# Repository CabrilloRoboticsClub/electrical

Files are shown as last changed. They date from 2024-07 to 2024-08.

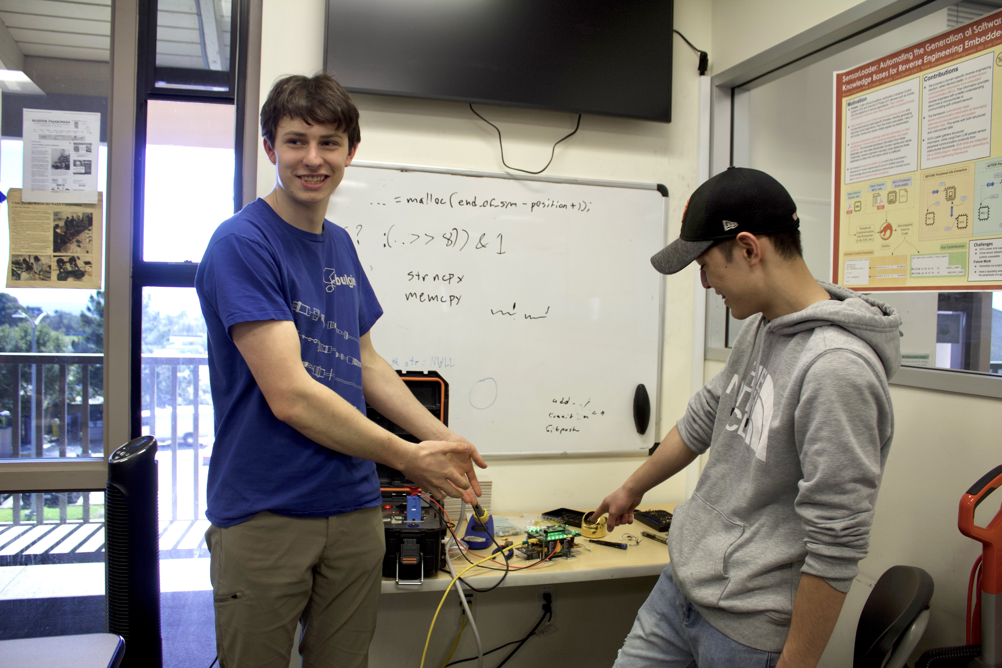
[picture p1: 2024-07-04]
Photos/Electrical_Team_Cellbrating_First_Full_Power_UpWithNoSmoke.jpg

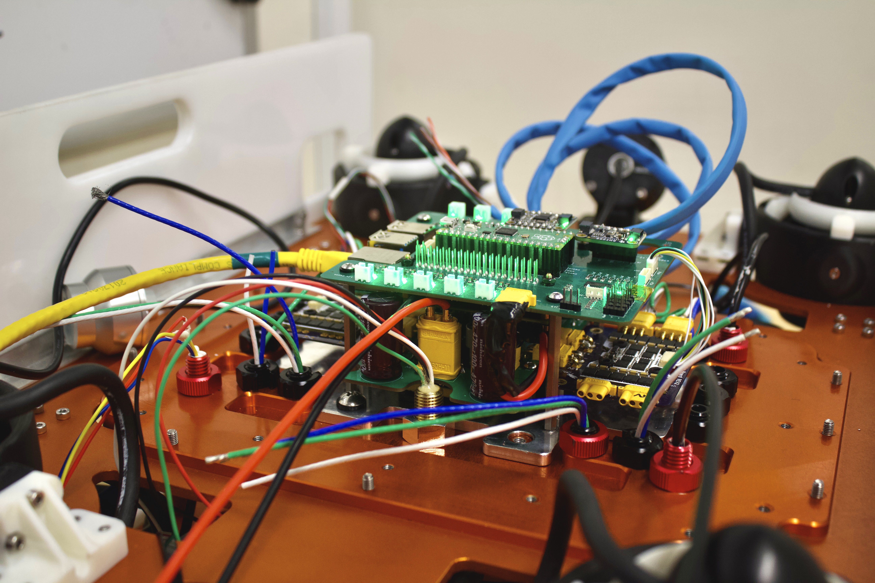
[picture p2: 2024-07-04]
Photos/FirstPowerUpOnROV.jpg

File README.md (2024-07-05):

# MATE ROV Electrical Stack for 2024 ROV Seahawk II

## Overview
This year, we decided to develop a stack of custom boards for the first time. We made this decision to reduce the size and weight of the Seahawk II while also improving overall durability, reliability, and power consumption. In the past, wiring harnesses were a significant point of failure, so we aimed to reduce their use.

## Intorduction
ectrical_Box_Stack_Overview Photo


The Seahawk II electrical stack focuses on high integration. We reduced the number of boards to three, which all connect seamlessly. This minimized space requirements. While the R&D expenses for developing these boards were high, the completed stack is incredibly reliable and significantly reduces costs compared to off-the-shelf options.

## For exstive documetaion go to the wiki

https://github.com/CabrilloRoboticsClub/electrical/wiki

### Members of 2024 electrical team:
- Isaac Wax
- Isaac Eda

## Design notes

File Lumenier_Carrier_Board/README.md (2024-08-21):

# Lumenier ESC Carrier Board
https://github.com/CabrilloRoboticsClub/electrical/wiki/ESC-Carrier-Board

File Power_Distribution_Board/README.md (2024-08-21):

# Power Distrubtion Board
https://github.com/CabrilloRoboticsClub/electrical/wiki/Power-Distribution-Boad

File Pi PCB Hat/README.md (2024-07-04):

# Pi PCB Hat

https://github.com/CabrilloRoboticsClub/electrical/wiki/Pi-Hat-PCB

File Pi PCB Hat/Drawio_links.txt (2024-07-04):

RPI Hat
https://drive.google.com/file/d/1-mpWdMjtuBn4qCpJHgUvGb3abJFzCt9e/view?usp=sharing

Bus lines Pi Hat PCB
https://drive.google.com/file/d/16jqgarMsz4_aKGhgsrGLv56VGpTJN2zc/view?usp=sharing

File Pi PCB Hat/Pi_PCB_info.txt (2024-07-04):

This .txt serves as general purpose information, as well as a checklist. Therefore every major connection/interaction must be listed here. by Isaac Eda

RPI Headers
- This is the interface for the Raspberry Pi 4(RPi 4)
- Supply Power: The Pi itself is powered by 5V through its USB port. No need for power input through the Pi hat PCB board.
- I2C: The two I2C ports, SDA and SCL are extended through the PCB as BUS lines. Multiple devices connect to this BUS.
- UART: The Pico W is connected to the Pi 4 via UART
- Power Supplied(to other devices): Supplies 3.3V logic power to the BNO05 and BME280. Also supplies 5V logic power to the PCA9685 PWM chip.
- Signal: Handles multiple inputs/outputs via GPIO to multiple devices, including; GPIO output for Power Switching Mosfets, output for BNO05 reset, input for BNO05 interrupt pin, input for BME280 Data, output for Pico W reset transistor switch, output for PCA9685 OE(output enable) pin.

Power Switching
- This is for switching on/off the relatively large power from the Power Board PCB, whether it's 12V or 5V. Multiples of this circuit may be present on the Pi PCB. Multiple may even branch out from the same power BUS line.
- Supply Power: Either 12V or 5V, supplied by the Power board PCB. 
- Signal: takes GPIO from RPi 4, to turn mosfet on/off
- Power Supplied: (Multiple)Solenoid valves for switching pneumatics, miscellaneous 5V tooling.

BNO05
- Inertial Measurement Unit(IMU)
- Supply Power: Takes 3.3V logic power
- I2C: Connected via I2C SDA and SCL
- Signal: GPIO input for reset, GPIO output for configurable Hardware interrupt. Also a solderable jumper pad connected to supply power to change I2C address is included on the Pi hat PCB.

BME280
- Humidity Sensor
- Supply Power: Takes 3.3V logic power
- I2C: Connected via I2C SDA and SCL
- Signal: GPIO output for data

PICO W Headers
- Supply Power: The Pico W is powered by 5V through its USB port. No need for input power through the Pi hat PCB board. 
- I2C: Connected via I2C SDA and SCL
- UART: Connected to RPi 4 via UART RX and TX
- Power Supplied(to other devices): 

PCA9685 PWM
-

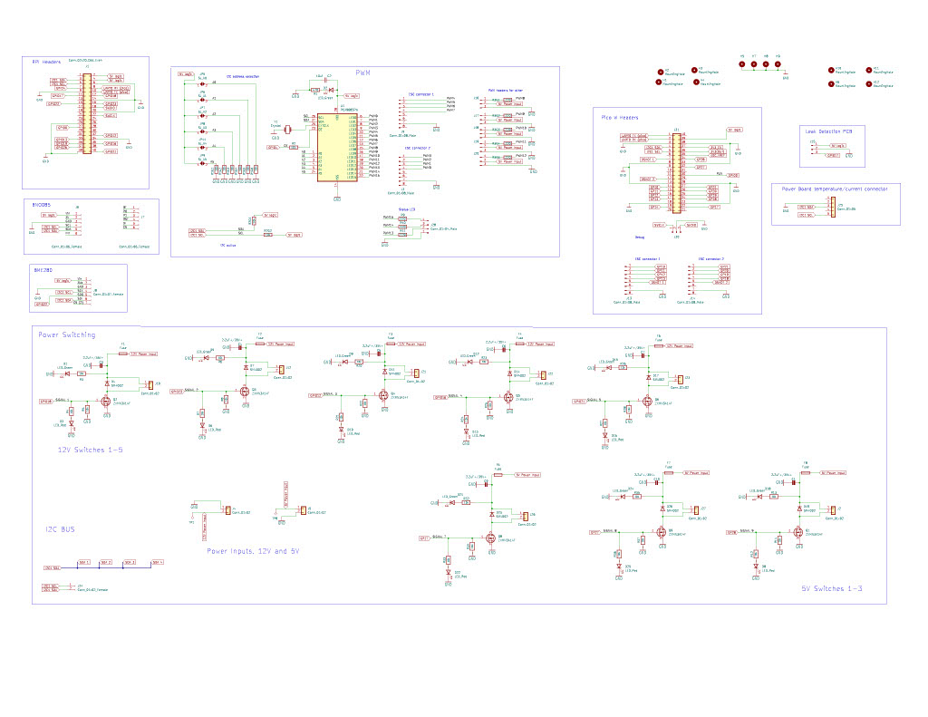
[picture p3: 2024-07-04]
Pi PCB Hat/Pi_Hat_Schematic.jpg

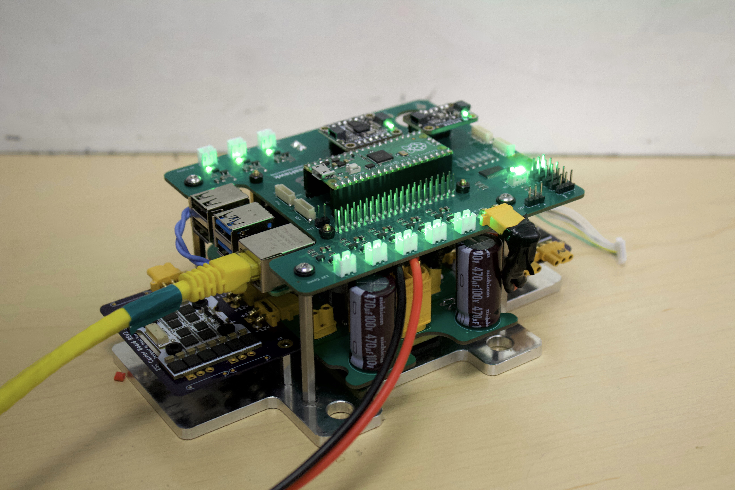
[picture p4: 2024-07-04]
Photos/FirstPowerUp.jpg

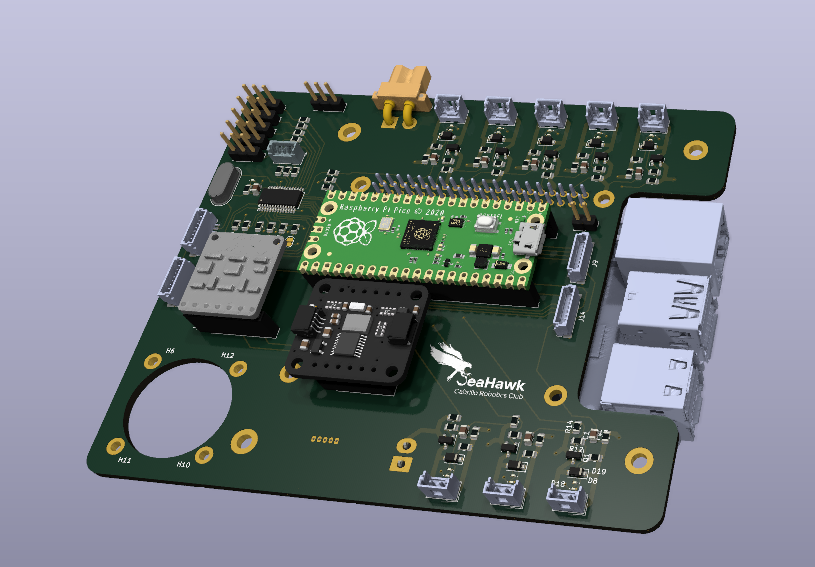
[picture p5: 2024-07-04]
Photos/Screenshot 2024-05-08 224635.png

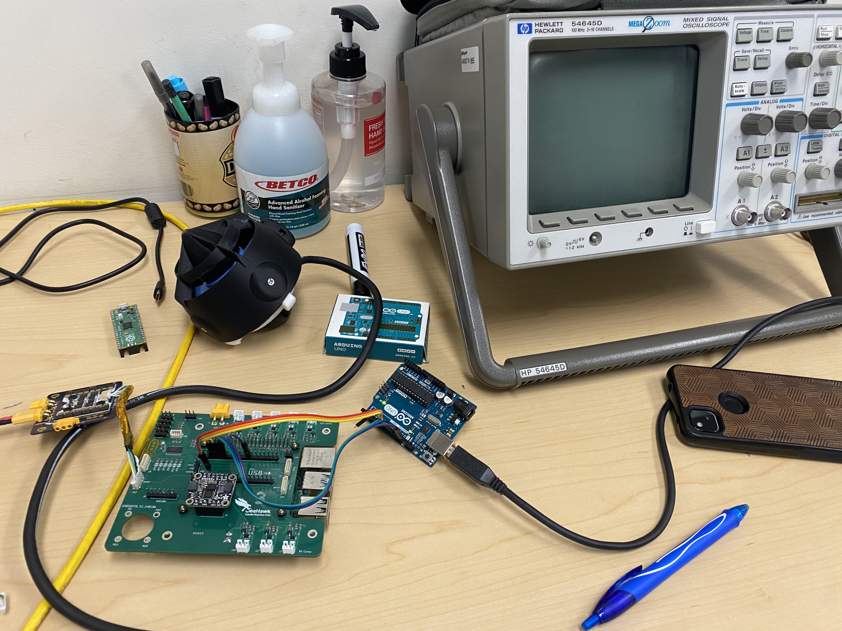
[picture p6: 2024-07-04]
Photos/ProgramingESCBoards.jpg

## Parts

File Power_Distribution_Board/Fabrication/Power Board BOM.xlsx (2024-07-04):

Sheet: Power Board
Ref | Qnty | Value | Cmp name | Footprint | Description | Vendor | Link | Coust | Total | Orderd
C1, C2, C3, C4, C5, | 5 | 470 uF | C_Polarized_Small_US | 470UF CAP:CAP_EEHZU1V471V | Polarized capacitor, small US symbol | Mouser | https://www.mouser.com/ProductDetail/Panasonic/EEH-ZU1V471V?qs=iLbezkQI%252BshMA5Itlz568g%3D%3D | 2.5 | 12.5 | 12 arived
 |  |  |  |  |  |  |  |  | 0
C6, C7, C8, C9, C10, | 5 | 220 uF | C_Polarized_Small_US | 220UF CAP:CAP_EEHZU1H221V | Polarized capacitor, small US symbol | Mouser | https://www.mouser.com/ProductDetail/Panasonic/EEH-ZU1H221V?qs=iLbezkQI%252BsiexANYtbJdHQ%3D%3D | 2.5 | 12.5 | 12 arived
 |  |  |  |  |  |  |  |  | 0
C11, C12, | 2 | 330 uF | C_Polarized_Small_US | 220UF CAP:CAP_16SVPG330MX | Polarized capacitor, small US symbol | Digkey | https://www.digikey.com/en/products/detail/panasonic-electronic-components/16SVPG330M/11200070 | 1.73 | 3.46
 |  |  |  |  |  |  |  |  | 0
J1, | 1 | Conn_01x02 | Conn_01x02 | Connector_AMASS:AMASS_XT30U-M_1x02_P5.0mm_Vertical | Generic connector, single row, 01x02, script generated (kicad-library-utils/schlib/autogen/connector/) | Amazon | https://www.amazon.com/Banana-Connector-Upgraded-Battery-Quadcopter/dp/B07PZ13CHC |  | 10.99 | Arived
 |  |  |  |  |  |  |  |  | 0
J3, J4, J6, J7, J8, J9, | 6 | Conn_01x02 | Conn_01x02 | Connector_AMASS:AMASS_XT30PW-M_1x02_P2.50mm_Horizontal | Generic connector, single row, 01x02, script generated (kicad-library-utils/schlib/autogen/connector/) | Ebay | https://www.amazon.com/gp/product/B099F2PXYN/ref=ppx_yo_dt_b_asin_title_o00_s00?ie=UTF8&psc=1 | 9.59 | 9.59 | Arived
 |  |  |  |  |  |  |  |  | 0
J5, | 1 | Conn_01x05 | Conn_01x05 | Connector_Molex:Molex_PicoBlade_53047-0510_1x05_P1.25mm_Vertical | Generic connector, single row, 01x05, script generated (kicad-library-utils/schlib/autogen/connector/) | Mouser | https://www.mouser.com/ProductDetail/Molex/53047-0510?qs=KC2ywxza1koXSHAr3dqR%2FQ%3D%3D | 0.39 | 0.39
 |  |  |  |  |  |  |  |  | 0
J10, J11, | 2 | Conn_01x02 | Conn_01x02 | Connector_Molex:Molex_KK-396_A-41791-0002_1x02_P3.96mm_Vertical | Generic connector, single row, 01x02, script generated (kicad-library-utils/schlib/autogen/connector/) | Digkey | https://www.digikey.com/en/products/detail/molex/0009484028/863363?s=N4IgTCBcDaIAxwJwBYAcy5lSAugXyA | 0.78 | 1.56
 |  |  |  |  |  |  |  |  | 0
R1, R2, | 2 | R | R | Resistor_SMD:R_2512_6332Metric_Pad1.40x3.35mm_HandSolder | Resistor | N/A | N/A |  | 0
 |  |  |  |  |  |  |  |  | 0
U1, | 1 | BMR4800102/002 | BMR4800102/002 | Power Bricks:bmr480-45-to-60vin-12vout-900w |  | Digkey | https://www.digikey.com/en/products/detail/flex-power-modules/BMR4800102-002/10287640 | 152.94 | 129.07 | Arived
 |  |  |  |  |  |  |  |  | 0
U2, | 1 | PKU3511SPI | PKU3511SPI | Footprints:PKU 3500S_FPM |  | Digkey | https://www.digikey.com/en/products/detail/flex-power-modules/PKU3511SPI/10287636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 | 56.46 | 56.46
Zener diode |  |  |  |  |  |  |  |  | 236.52
R3
~~PCB Manufacturing Survices~~ | ~~coust~~ | ~~notes~~
~~JLC PCB~~ | ~~18.30 + shipping ~~ | ~~5X, 2oz copper~~
~~PCB Way~~ | ~~56.68 total~~ | ~~2 oz copper, 5X, any silkscreen coller~~
~~Allpcb~~
~~bayareacircuits~~
OSH Park | 53.65 | 2 oz cupper, .8mm +shipping

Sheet: Lumenier Carrier Board
Ref | Qnty | Value | Cmp name | Footprint | Description | Vendor | Link | Coust | Total | Orderd
~~H1, H2,~~ | ~~2~~ | ~~MountingHole~~ | ~~MountingHole~~ | ~~MountingHole:MountingHole_3.2mm_M3_ISO14580_Pad~~ | ~~Mounting Hole without connection~~ | ~~N/A~~ | ~~N/A~~
J1, J2, J3, J4, | 4 | Conn_01x03 | Conn_01x03 | Connector_AMASS:AMASS_MR30PW-FB_1x03_P3.50mm_Horizontal | Generic connector, single row, 01x03, script generated (kicad-library-utils/schlib/autogen/connector/) | Ebay | https://www.ebay.com/itm/174074480926 | 8.98 | 29 | Yes, Will be here by the 29th
J5, J6, | 2 | Conn_01x02 | Conn_01x02 | Connector_AMASS:AMASS_XT30PW-F_1x02_P2.50mm_Horizontal | Generic connector, single row, 01x02, script generated (kicad-library-utils/schlib/autogen/connector/) | Amazon | See in power board BOM
U1, | 1 | Lumenier_Mini_Razor_Pro_ESC | Lumenier_Mini_Razor_Pro_ESC | Footprints:Lumenier_Mini_Razor_Pro_ESC |  | GetFPV | https://www.getfpv.com/lumenier-mini-razor-pro-4in1-20x20-f3-blheli-32-45a-2-6s-esc.html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 | 59.99 | 69.8 | Orderd one a few months ago on club card
 |  |  |  |  |  |  |  |  | 98.8
 |  |  |  |  |  |  |  |  | total board coust
 |  |  |  |  |  |  |  |  | 107.0833333
Board for OSH park | 3X | 24.85
 |  | 8.283333333

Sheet: REV B Order List
Description | Vendor | Link | Coust | Qnty | Total | Orderd
BMR4800102/002 | Digkey | https://www.digikey.com/en/products/detail/flex-power-modules/BMR4800102-002/10287640 | 135.46 | 3 | 406.38
2166-PKU3511SPI-ND | Digkey | https://www.digikey.com/en/products/detail/flex-power-modules/PKU3511SPI/10287636 | 56.46 | 2 | 112.92
Lumenier Mini Razor Pro 4in1 20x20 F3 BLHeli_32 45A 2-6s ESC | GetFPV | https://www.getfpv.com/lumenier-mini-razor-pro-4in1-20x20-f3-blheli-32-45a-2-6s-esc.html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 | 59.99 | 3 | 179.97
Soalder Paste |  |  |  |  | 0
Low Temp Soalder |  |  |  |  | 0
 |  |  |  |  | 0
 |  |  |  |  | 0
 |  |  |  |  | 0
 |  |  |  |  | 0
 |  |  |  |  | 0
 |  |  |  |  | 0
 |  |  |  |  | 0
 |  |  |  |  | 0
 |  |  |  |  | 0
 |  |  |  |  | 0
 |  |  |  |  | 0
 |  |  |  |  | 0
 |  |  |  |  | 0
 |  |  |  |  | 0
 |  |  |  |  | 0
 |  |  |  |  | 0
 |  |  |  |  | 0
 |  |  |  |  | 0
 |  |  |  |  | 0
 |  |  |  |  | 699.27

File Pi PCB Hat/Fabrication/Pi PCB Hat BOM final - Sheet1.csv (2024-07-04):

Comment | Designator | Footprint | JLCPCB Part #（optional）
10k | R1G5,R37,R28,R14,R2,R34,R21,R7,R1G2,R6,R25,R1G3,R1G6,R32,R27,R13,R1G4,R12,R26,R5,R20,R33,R23,R1G1,R3,R2G2,R35,R36,R22,R4,R24,R8,R2G1 | R_0805_2012Metric | C25612
ZXMN3A14F | Q9,Q6,Q2,Q1,Q4,Q3,Q5,Q8 | SOT-23 | C88051
LED_Green | D24,D9,D2,D1,D5,D12,D21,D15,D18 | LED_0603_1608Metric | C12624
2.2uF+/35V+ | C3,C5,C7,C4,C6,C9,C1,C10 | C_0805_2012Metric | C377773
LED_Red | D10,D22,D3,D6,D16,D25,D8,D13 | LED_0603_1608Metric | C2286
220 | R3G2,R3G5,R3G3,R9,R10,R11,R3G4,R3G1 | R_0805_2012Metric | C25294
Fuse | F3,F2,F4,F8,F6,F1,F7,F5 | Fuse_0805_2012Metric | C2760264
SM4002 | D4,D19,D23,D26,D7,D14,D11,D17 | D_SOD-123F | C169542
PCA9685PW | U1 | TSSOP-28_4.4x9.7mm_P0.65mm | C2678753
10uf | C2 | C_0805_2012Metric | C15850
470 | R1 | R_0805_2012Metric | C229215

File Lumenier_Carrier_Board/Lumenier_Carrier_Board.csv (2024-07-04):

Source: | C:\Users\Isac\Nextcloud\Electrical\E_CAD\Lumenier_Carrier_Board\Lumenier_Carrier_Board.kicad_sch
Date: | 9/13/2023 9:21:46 AM
Tool: | Eeschema (6.0.5)
Generator: | C:\Program Files\KiCad\6.0\bin\scripting\plugins/bom_csv_grouped_by_value_with_fp.py
Component Count: | 9
Ref | Qnty | Value | Cmp name | Footprint | Description | Vendor
H1, H2, | 2 | MountingHole | MountingHole | MountingHole:MountingHole_3.2mm_M3_ISO14580_Pad | Mounting Hole without connection
J1, J2, J3, J4, | 4 | Conn_01x03 | Conn_01x03 | Connector_AMASS:AMASS_MR30PW-FB_1x03_P3.50mm_Horizontal | Generic connector, single row, 01x03, script generated (kicad-library-utils/schlib/autogen/connector/)
J5, J6, | 2 | Conn_01x02 | Conn_01x02 | Connector_AMASS:AMASS_XT30PW-F_1x02_P2.50mm_Horizontal | Generic connector, single row, 01x02, script generated (kicad-library-utils/schlib/autogen/connector/)
U1, | 1 | Lumenier_Mini_Razor_Pro_ESC | Lumenier_Mini_Razor_Pro_ESC | Footprints:Lumenier_Mini_Razor_Pro_ESC

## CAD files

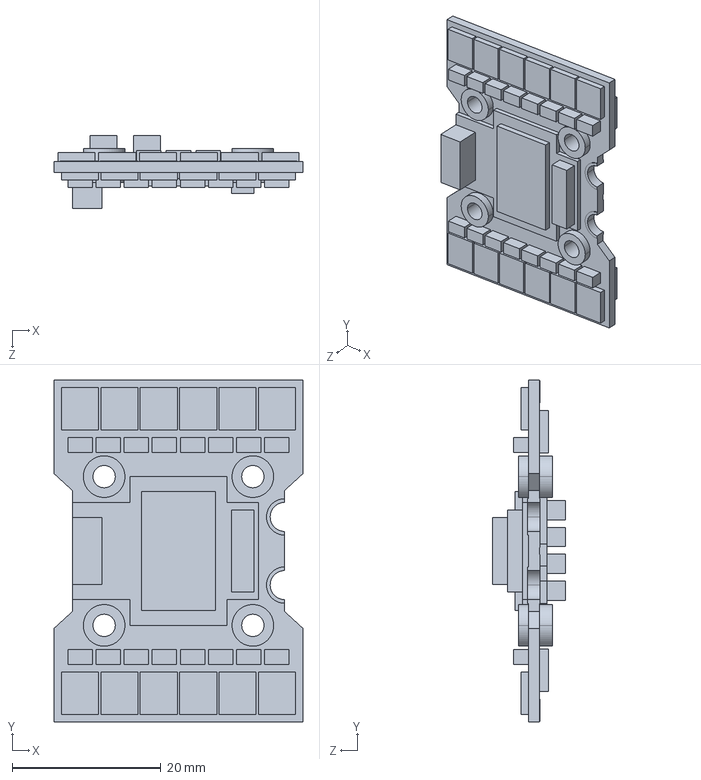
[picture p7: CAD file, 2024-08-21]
KICAD_EDA_Componet_Libarry/3D_Models/Lumenier_ESC.STEP
33.5 x 46.0 x 9.80 mm

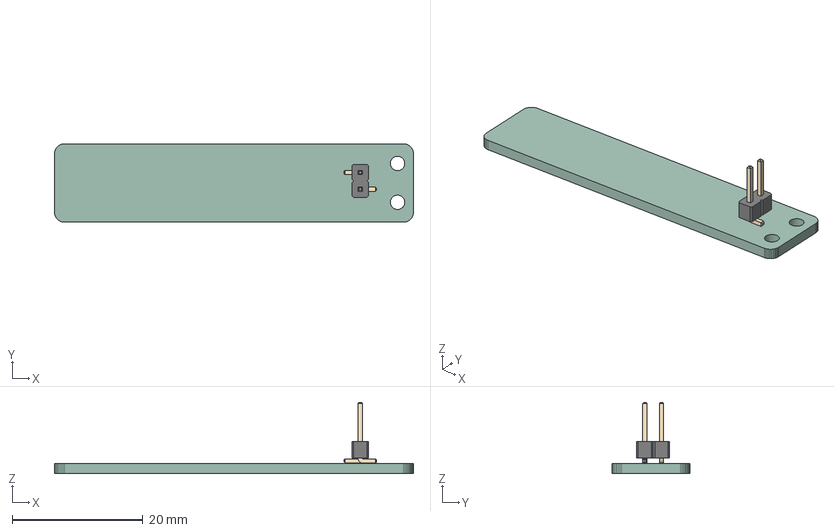
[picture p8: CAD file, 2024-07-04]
Leak_Detection_PCB/Leak_Detection_PCB.step
55.0 x 12.0 x 11.0 mm
PinHeader_1x02_P254mm_Vertical_SMD_Pin1Left
_autosave-Leak_Detection_PCB PCB

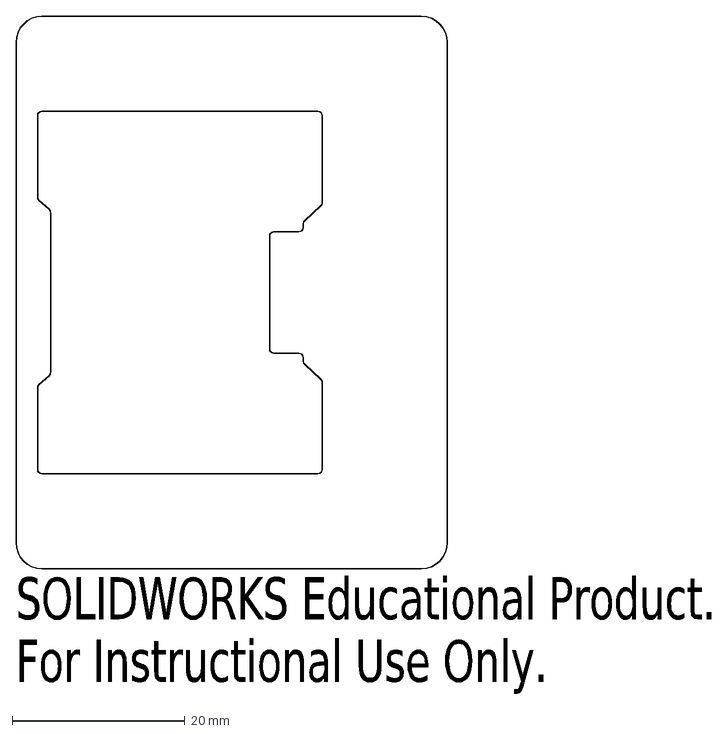
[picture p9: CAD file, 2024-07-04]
Lumenier_Carrier_Board/Lumenier_ESC_Carrier_Board_Outline_V3.DXF
SOLIDWORKS Educational Product.
For Instructional Use Only.

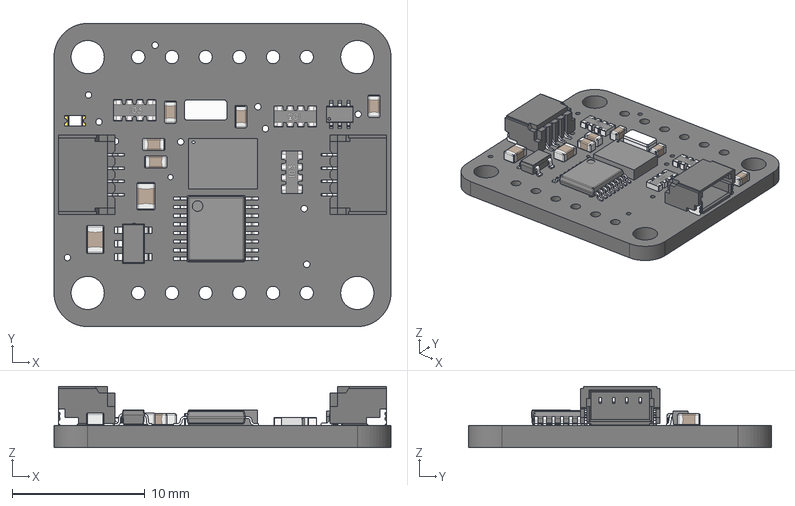
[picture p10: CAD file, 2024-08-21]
KICAD_EDA_Componet_Libarry/3D_Models/Adafruit BNO085 STEMMA QT.step
25.4 x 22.9 x 4.60 mm
Printed Circuit Board
BNO055-9axis-IMU
BNO085-9axis-IMU
BODY-TSSOP
LEAD-TSSOP x 16
Crystal_XTAL3215_32.768KHz
SOT23-5
BSS138PS
LED 0603 single color
CAPC-0805-T0.95-BN x 2
CAPC-0603-T0.9-BN x 5
YC164_RESPACK x 3
qwicc x 2

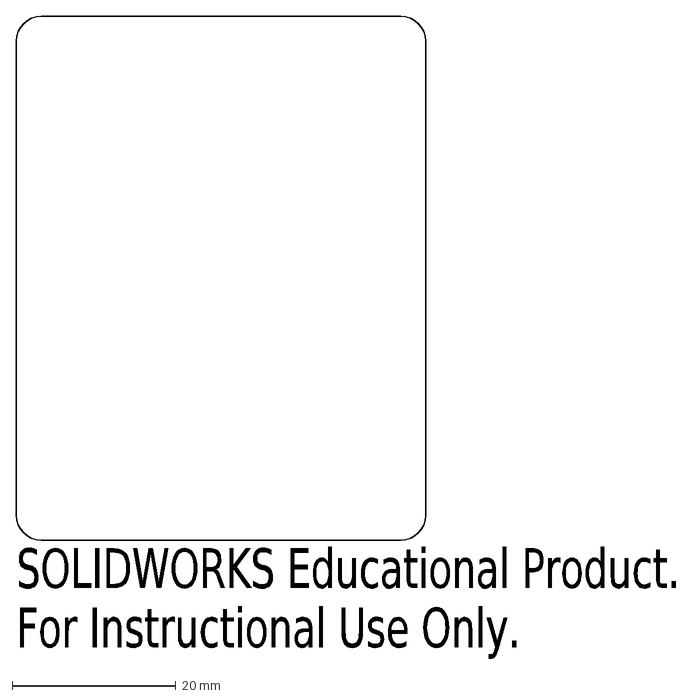
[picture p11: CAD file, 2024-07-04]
Lumenier_Carrier_Board/Lumenier_ESC_Carrier_Board_PCB_Outline.DXF
SOLIDWORKS Educational Product.
For Instructional Use Only.

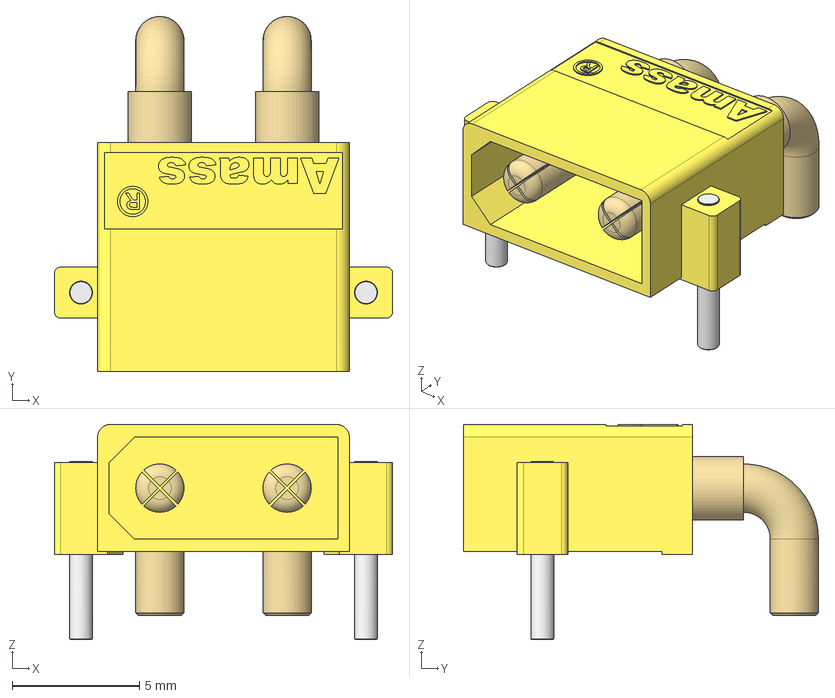
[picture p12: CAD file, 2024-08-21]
KICAD_EDA_Componet_Libarry/3D_Models/Amass_XT30PW-M_pcb solder.stp
13.3 x 13.9 x 8.45 mm

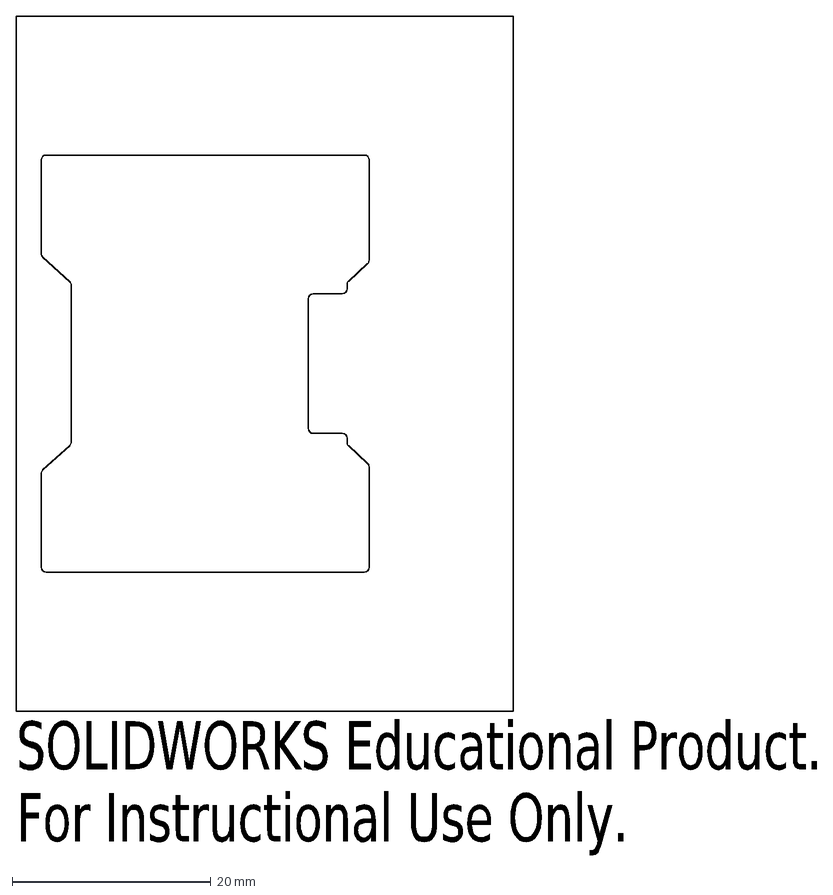
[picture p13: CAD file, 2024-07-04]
Lumenier_Carrier_Board/Lumenier_ESC_Carrier_Board_Outline.DXF
SOLIDWORKS Educational Product.
For Instructional Use Only.

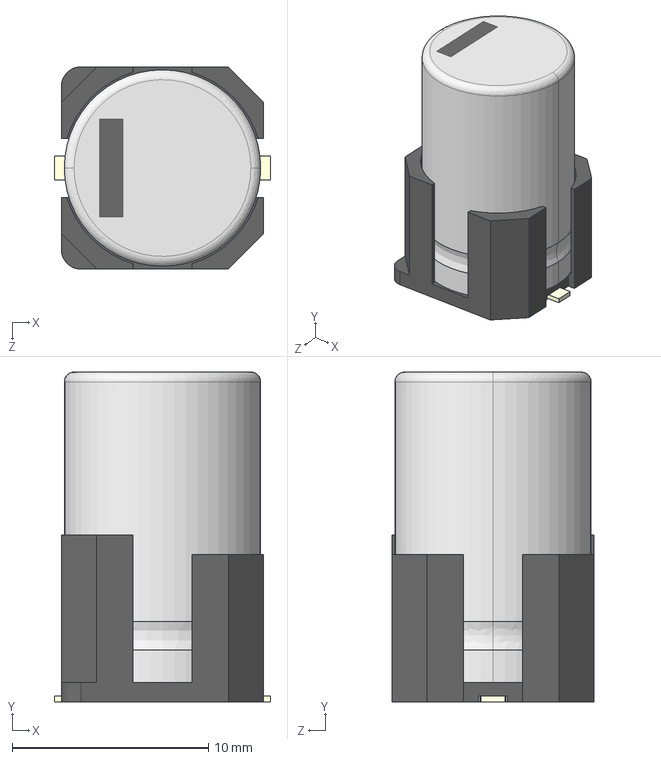
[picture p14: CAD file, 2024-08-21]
KICAD_EDA_Componet_Libarry/3D_Models/EEHZU1V471V.STEP
11.0 x 16.8 x 10.3 mm

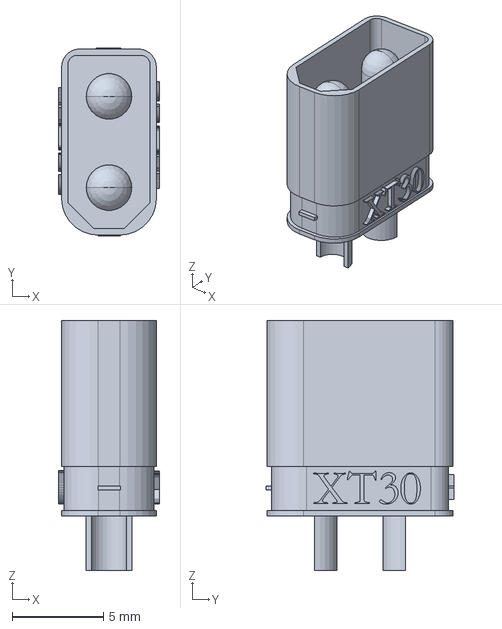
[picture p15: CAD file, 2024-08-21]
KICAD_EDA_Componet_Libarry/3D_Models/XT30-male.stp
5.54 x 10.3 x 13.7 mm

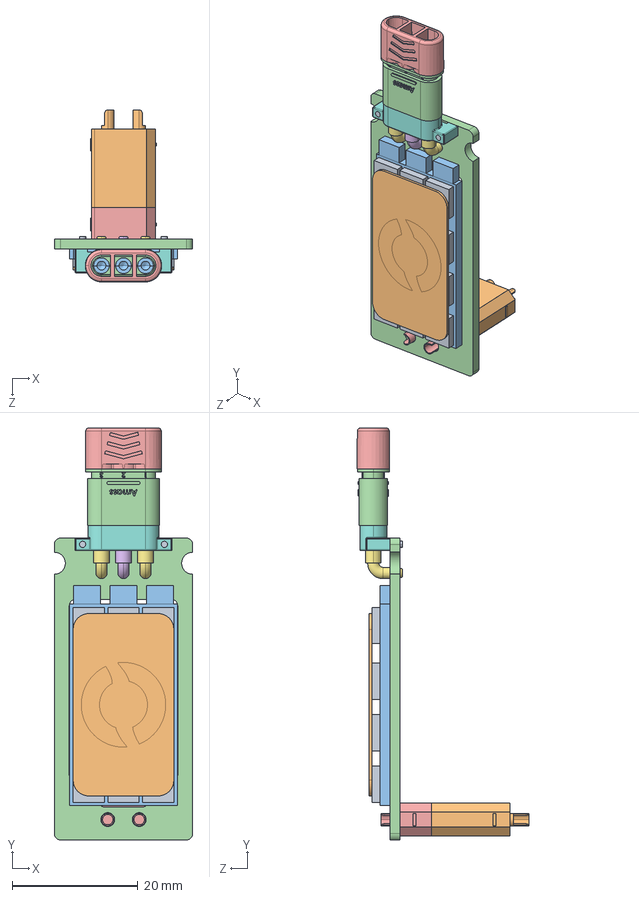
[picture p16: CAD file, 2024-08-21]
KICAD_EDA_Componet_Libarry/3D_Models/BESC_EXPANTION_BOARD.STEP
22.0 x 65.5 x 27.4 mm
BESC30-R3
BESC EXPANTION BOARD PCB
XT30 MALE
Amass MR30PW-FB_default
XT30_MALE_NEW
MR30_Femail

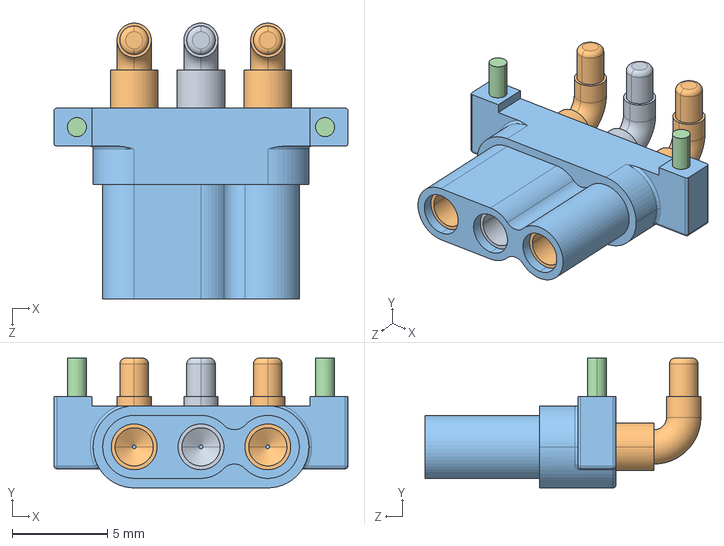
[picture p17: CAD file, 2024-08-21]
KICAD_EDA_Componet_Libarry/3D_Models/Amass MR30PW-FB.STEP
15.4 x 6.80 x 14.5 mm

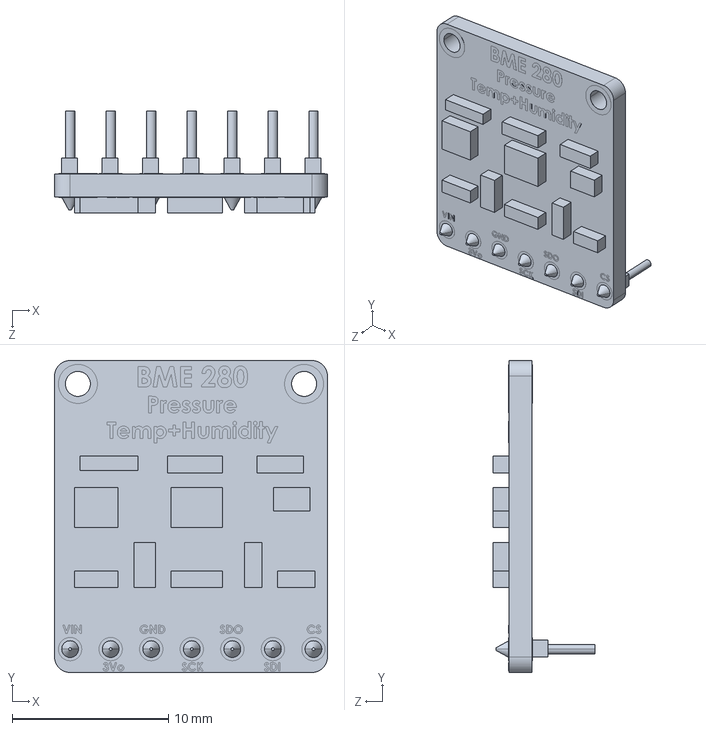
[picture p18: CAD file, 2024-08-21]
KICAD_EDA_Componet_Libarry/3D_Models/bme280.STEP
17.5 x 20.0 x 6.51 mm

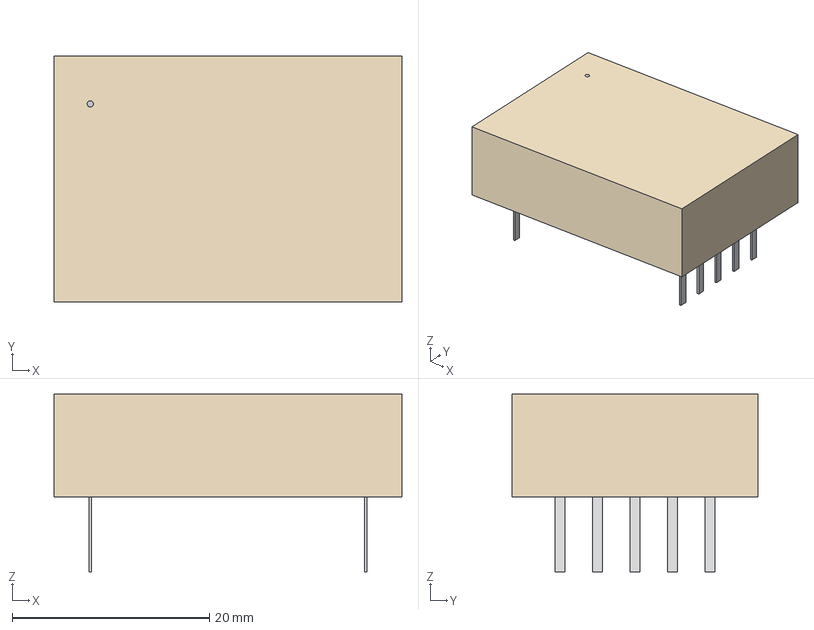
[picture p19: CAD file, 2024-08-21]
KICAD_EDA_Componet_Libarry/3D_Models/PKU3500S_FPM.step
35.3 x 25.0 x 18.0 mm

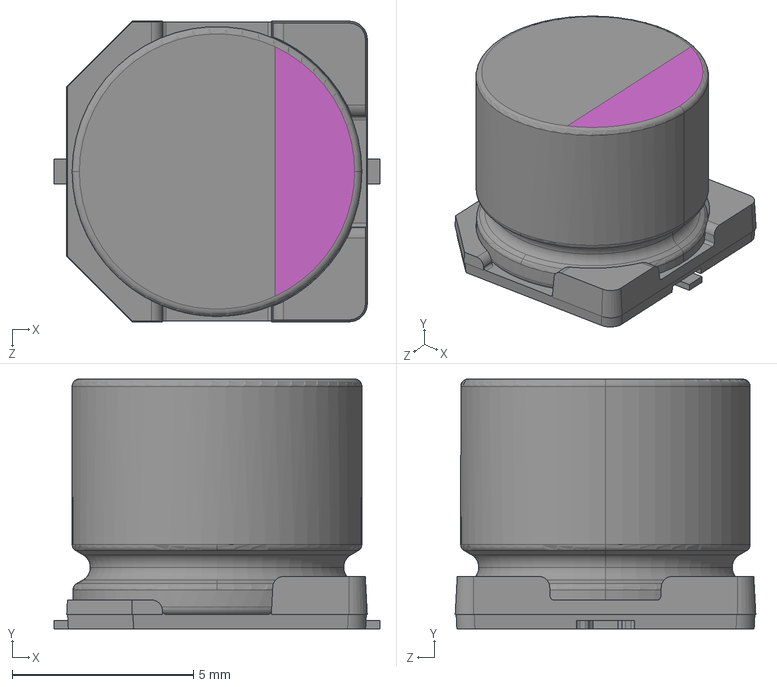
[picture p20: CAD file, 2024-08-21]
KICAD_EDA_Componet_Libarry/3D_Models/16SVPG330MX.step
9.00 x 6.90 x 8.30 mm

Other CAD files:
KICAD_EDA_Componet_Libarry/3D_Models/BM08B-SRSS-TB.STEP
KICAD_EDA_Componet_Libarry/3D_Models/XT30PW-F.STEP
KICAD_EDA_Componet_Libarry/3D_Models/Lumenier_Carrier_Board.step
KICAD_EDA_Componet_Libarry/3D_Models/009484028.stp
KICAD_EDA_Componet_Libarry/3D_Models/0530470510.step
KICAD_EDA_Componet_Libarry/3D_Models/530470410.stp
KICAD_EDA_Componet_Libarry/3D_Models/530470510.stp
KICAD_EDA_Componet_Libarry/3D_Models/53253-0270.STEP
KICAD_EDA_Componet_Libarry/3D_Models/53253-0270.stp

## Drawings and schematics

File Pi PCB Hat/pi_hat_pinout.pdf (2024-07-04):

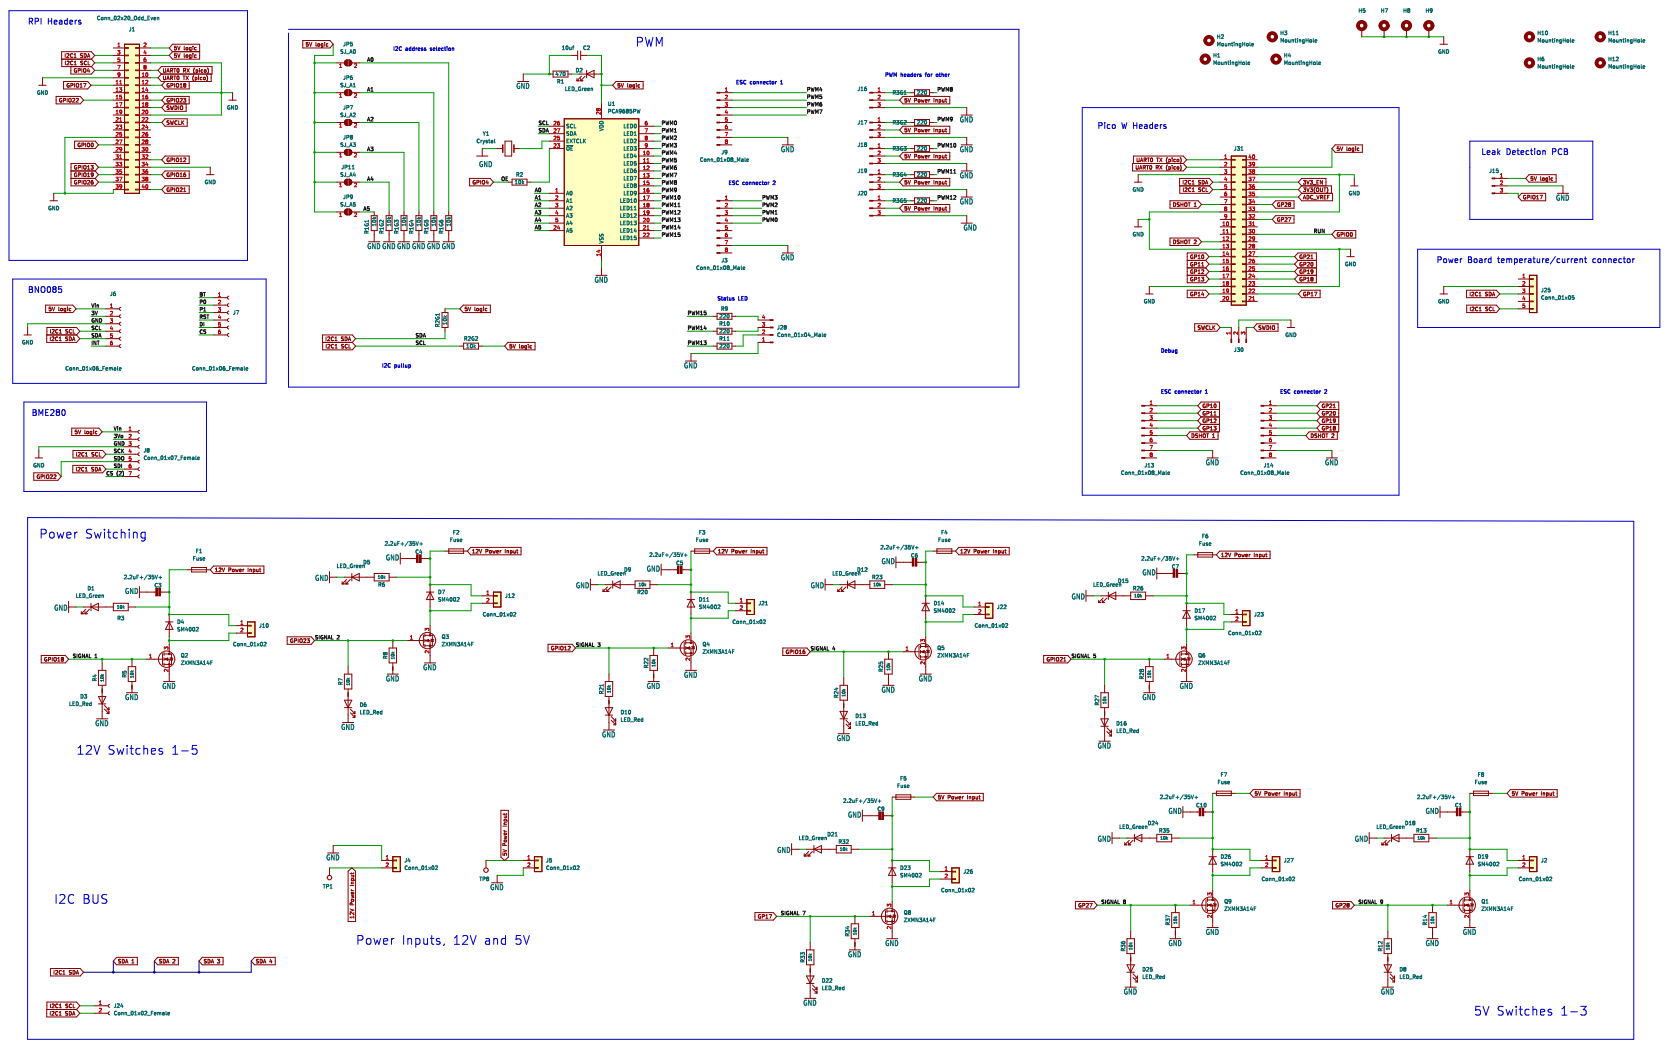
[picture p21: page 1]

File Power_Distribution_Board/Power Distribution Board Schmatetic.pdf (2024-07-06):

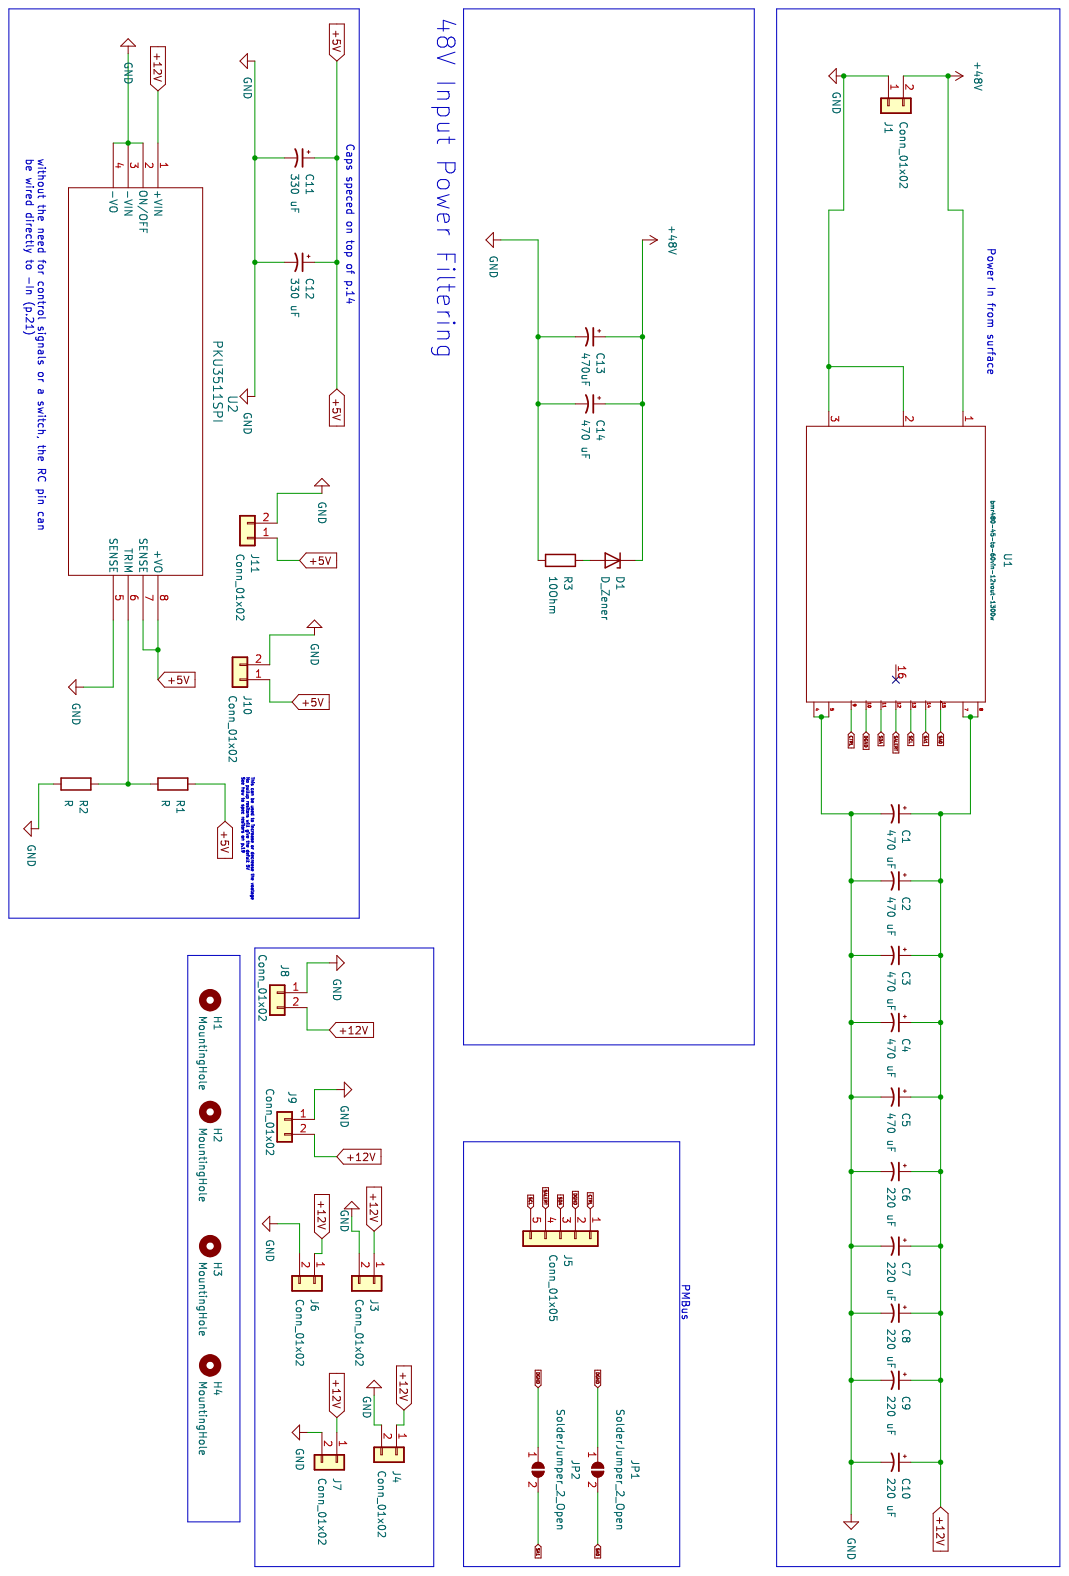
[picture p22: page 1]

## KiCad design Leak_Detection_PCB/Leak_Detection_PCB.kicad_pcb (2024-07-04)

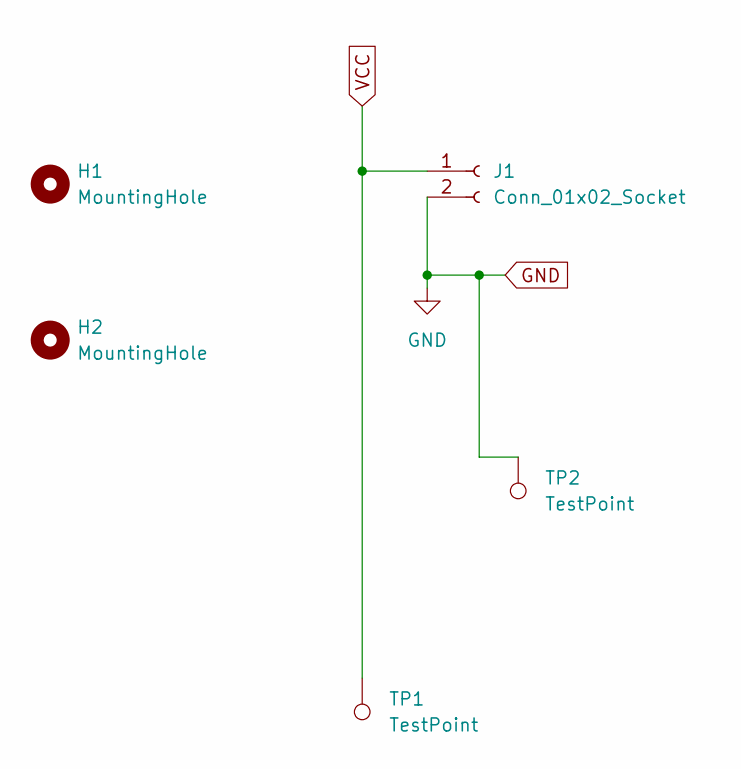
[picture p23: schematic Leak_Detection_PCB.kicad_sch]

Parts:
H1, H2: MountingHole; MountingHole_2.2mm_M2_Pad
J1: Conn_01x02_Socket; PinHeader_1x02_P2.54mm_Vertical_SMD_Pin1Left
TP1, TP2: TestPoint; TestPoint_Pad_D1.5mm

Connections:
GND: J1.2, TP2.1
VCC: J1.1, TP1.1

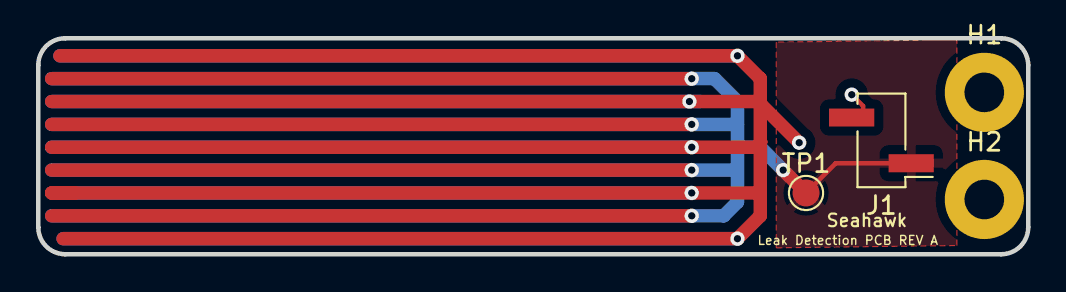
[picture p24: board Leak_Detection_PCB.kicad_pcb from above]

Board: 2 copper layers, 55.0 x 12.0 mm, 5 parts (1 on the bottom side), 2 nets.

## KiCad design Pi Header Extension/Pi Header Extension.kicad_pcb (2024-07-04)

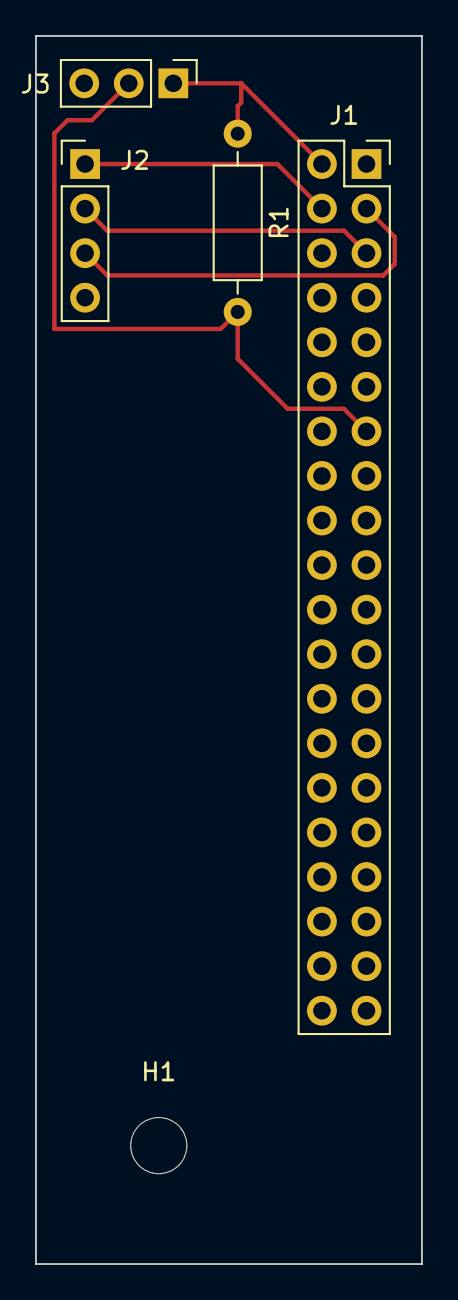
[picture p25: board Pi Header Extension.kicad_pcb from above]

Board: 2 copper layers, 22.0 x 70.0 mm, 5 parts (0 on the bottom side), 6 nets.

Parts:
H1: MountingHole; MountingHole_3.2mm_M3
J1: Conn_02x20_Odd_Even; PinSocket_2x20_P2.54mm_Vertical
J2: Conn_01x04_Pin; PinHeader_1x04_P2.54mm_Vertical
J3: Conn_01x03_Pin; PinHeader_1x03_P2.54mm_Vertical
R1: 4.7k; R_Axial_DIN0207_L6.3mm_D2.5mm_P10.16mm_Horizontal

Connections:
/5V: J1.2, J3.1, R1.1
/GND: J1.6, J1.14, J2.4, J3.3
/GPIO: J1.13, J3.2, R1.2
/SCL: J1.5, J2.2
/SDA: J1.3, J2.3
/Vin: J1.4, J2.1

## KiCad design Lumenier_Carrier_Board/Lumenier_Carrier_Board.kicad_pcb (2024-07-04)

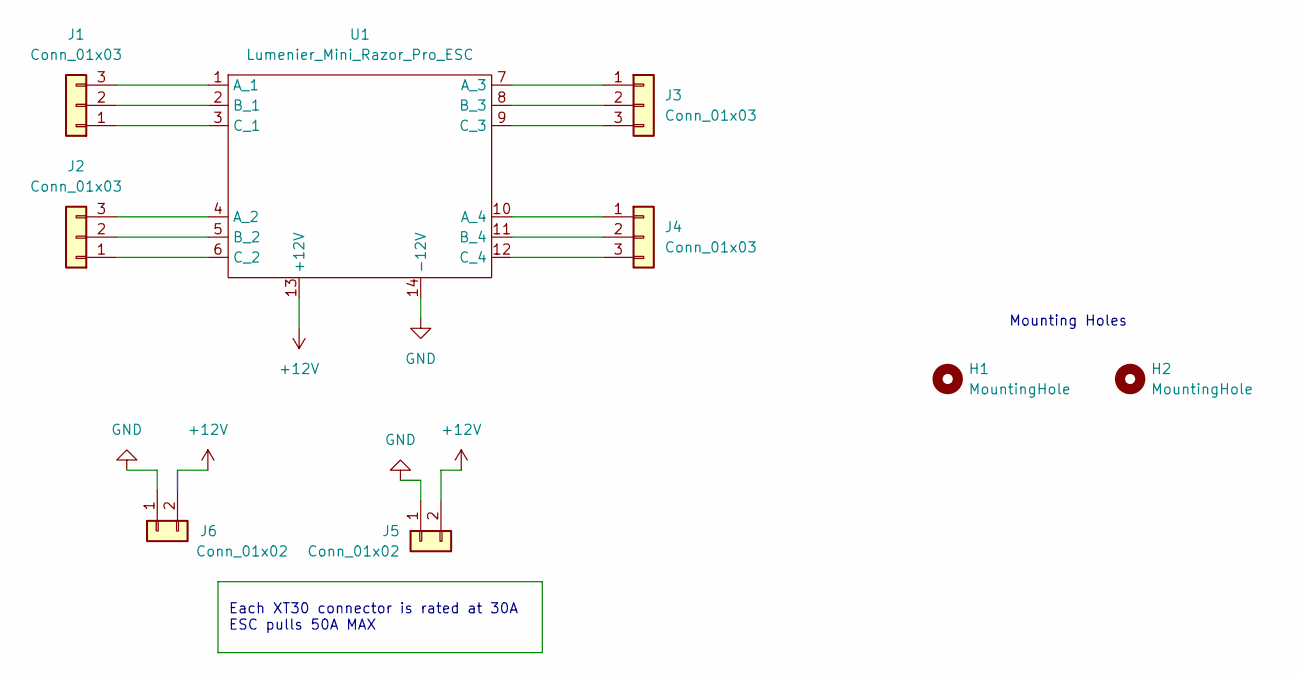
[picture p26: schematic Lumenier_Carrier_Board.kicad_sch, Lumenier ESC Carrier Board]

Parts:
H1, H2: MountingHole; MountingHole_3.2mm_M3_ISO14580_Pad
J1, J2, J3, J4: Conn_01x03; AMASS_MR30PW-FB_1x03_P3.50mm_Horizontal
J5, J6: Conn_01x02; AMASS_XT30PW-F_1x02_P2.50mm_Horizontal
U1: Lumenier_Mini_Razor_Pro_ESC

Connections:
+12V: J5.2, J6.2, U1.13 (+12V)
GND: J5.1, J6.1, U1.14 (-12V)
unnamed: J1.1, U1.3 (C_1)
unnamed: J1.2, U1.2 (B_1)
unnamed: J1.3, U1.1 (A_1)
unnamed: J2.1, U1.6 (C_2)
unnamed: J2.2, U1.5 (B_2)
unnamed: J2.3, U1.4 (A_2)
unnamed: J3.1, U1.7 (A_3)
unnamed: J3.2, U1.8 (B_3)
unnamed: J3.3, U1.9 (C_3)
unnamed: J4.1, U1.10 (A_4)
unnamed: J4.2, U1.11 (B_4)
unnamed: J4.3, U1.12 (C_4)

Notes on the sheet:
Mounting Holes
Each XT30 connector is rated at 30A ESC pulls 50A MAX

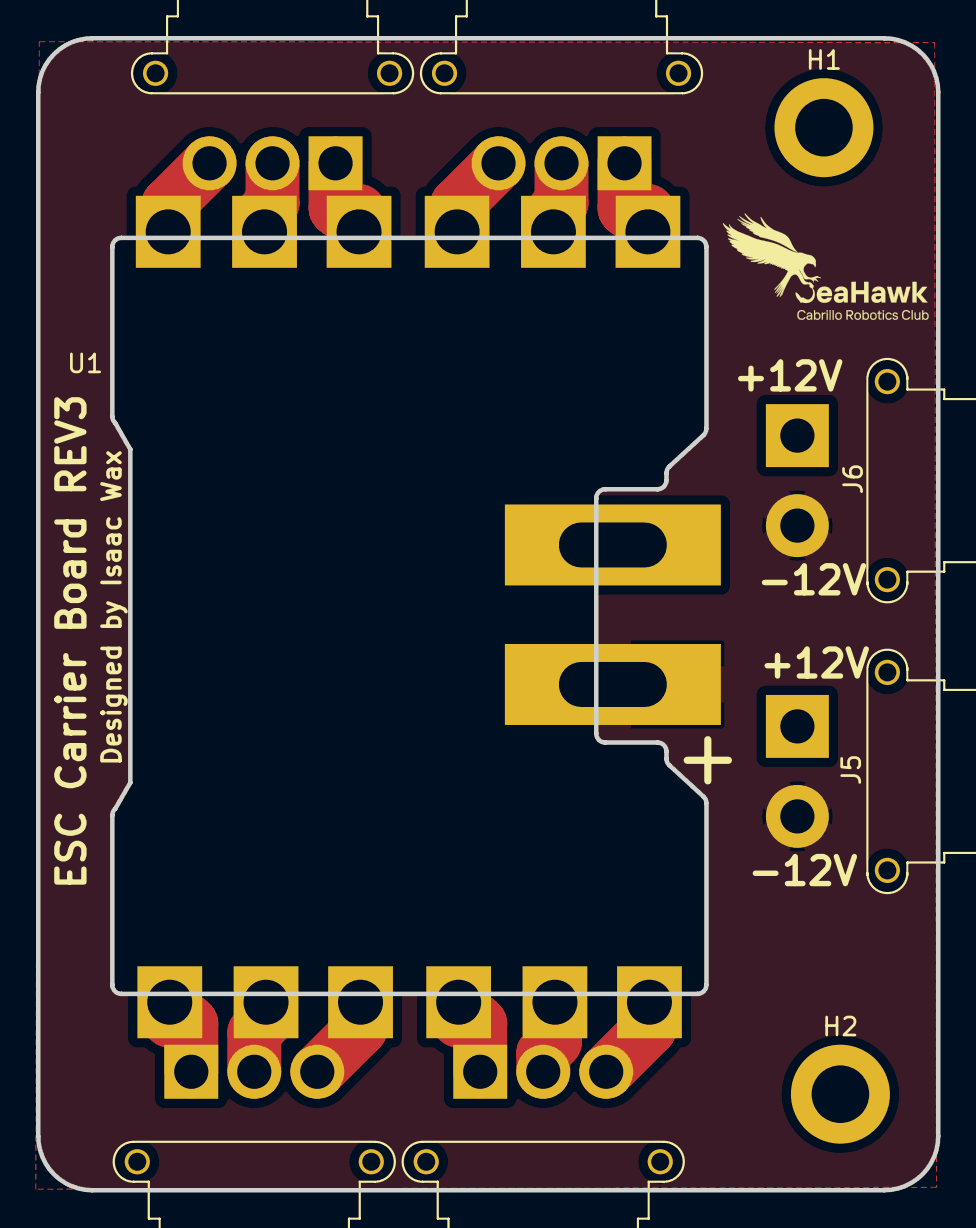
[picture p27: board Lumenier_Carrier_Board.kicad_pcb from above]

Board: 2 copper layers, 50.0 x 64.0 mm, 9 parts (0 on the bottom side), 14 nets.

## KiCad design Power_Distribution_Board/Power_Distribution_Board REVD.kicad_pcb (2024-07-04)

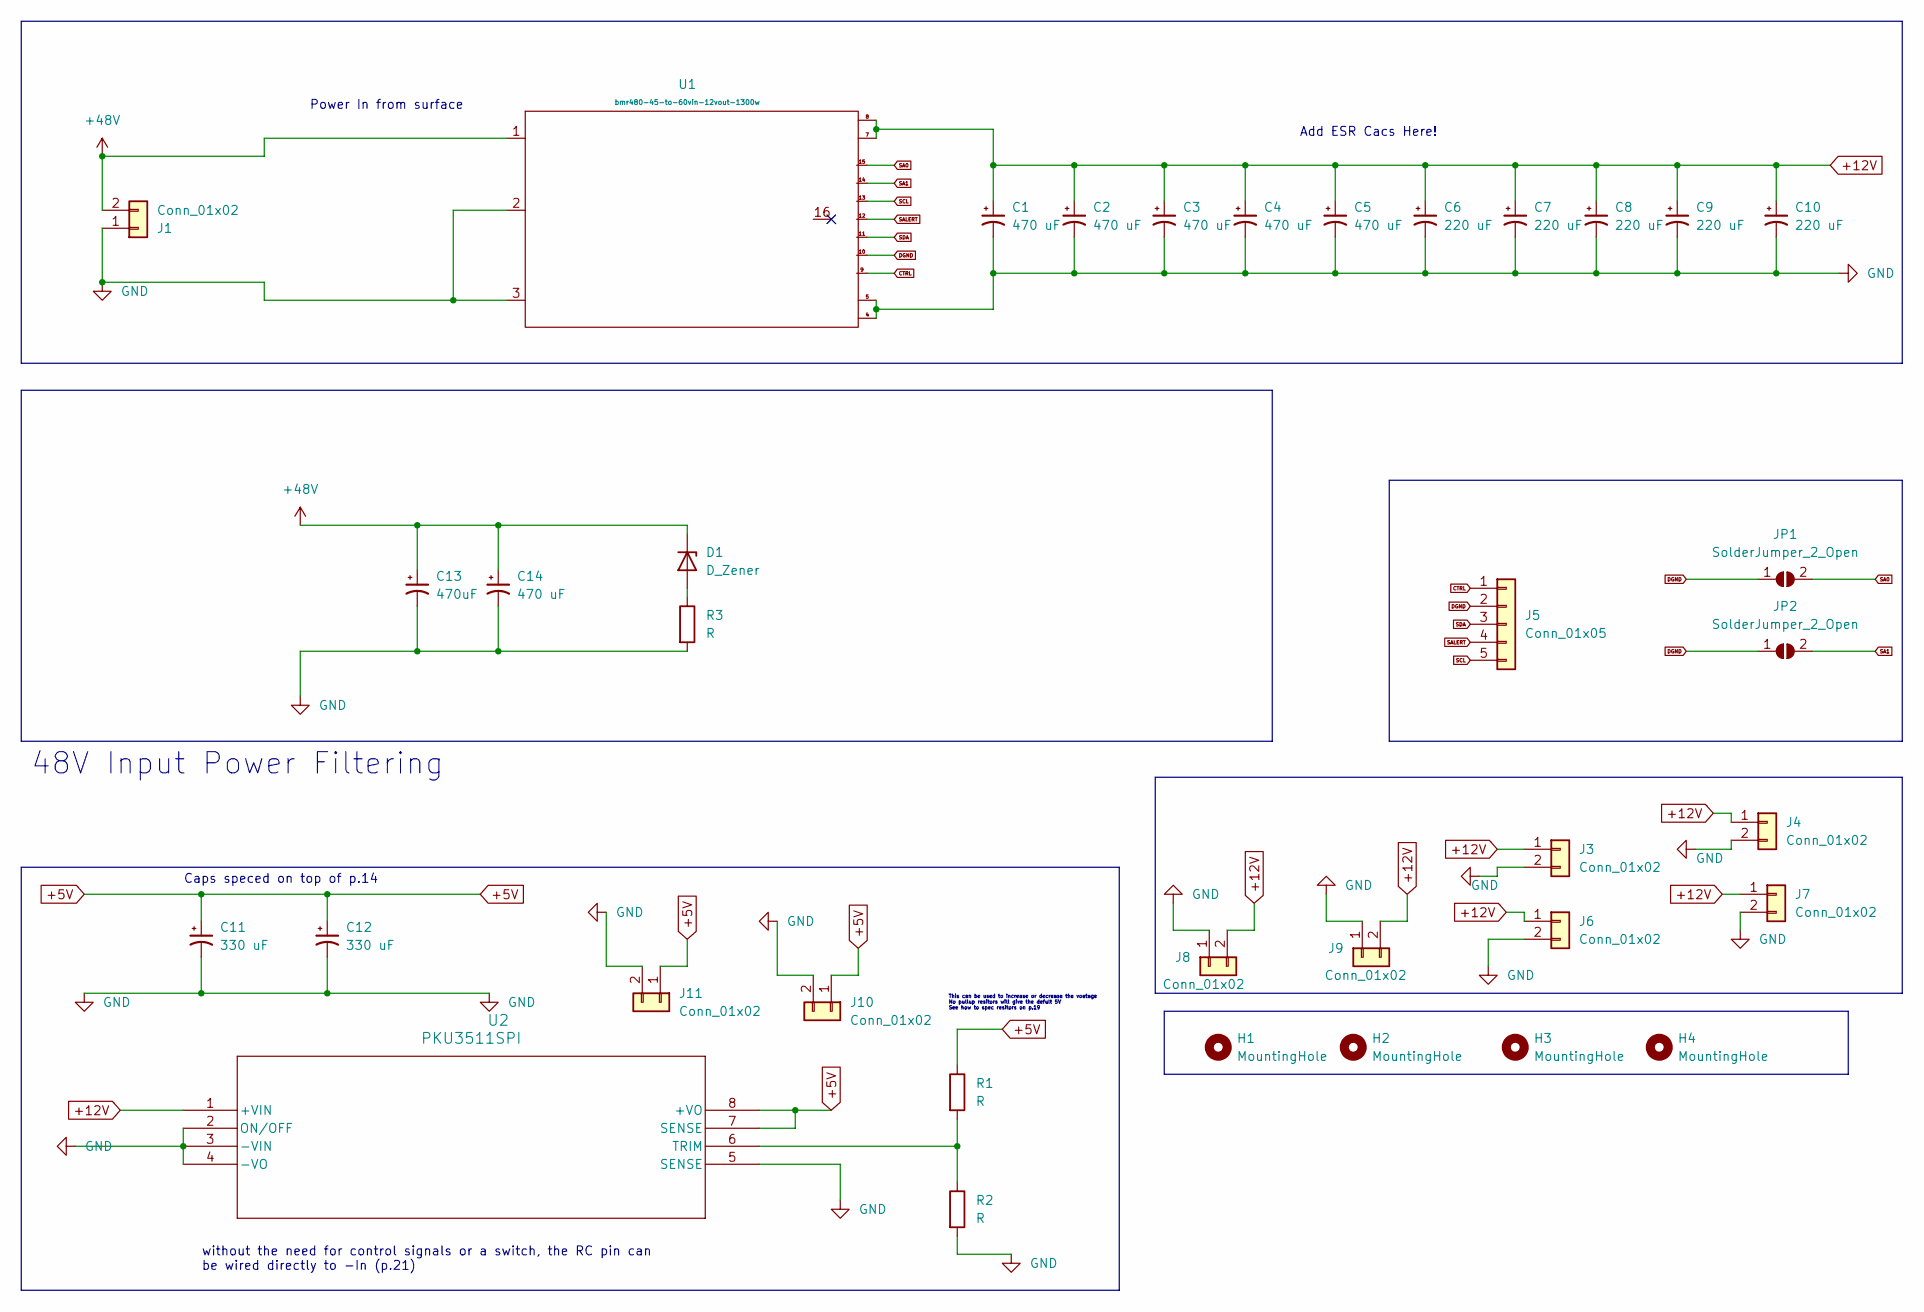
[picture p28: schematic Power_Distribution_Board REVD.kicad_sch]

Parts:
C1, C2, C3, C4, C5: 470 uF; CAP_EEHZU1V471V
C6, C7, C8, C9, C10: 220 uF; CAP_EEHZU1H221V
C11, C12: 330 uF; CAP_16SVPG330MX
C13: 470uF; PCAP_16x31.5-THRU-ELECT_NCA
C14: 470 uF; PCAP_16x31.5-THRU-ELECT_NCA
D1: D_Zener; D_DO-41_SOD81_P10.16mm_Horizontal
H1, H2, H3, H4: MountingHole; MountingHole_3.2mm_M3_DIN965_Pad
J1: Conn_01x02; AMASS_XT60-M_1x02_P7.20mm_Vertical
J3, J4, J6, J7: Conn_01x02; AMASS_XT30PW-M_1x02_P2.50mm_Horizontal
J5: Conn_01x05; Molex_PicoBlade_53047-0510_1x05_P1.25mm_Vertical
J8, J9: Conn_01x02; AMASS_XT30U-F_1x02_P5.0mm_Vertical
J10, J11: Conn_01x02; Molex_KK-396_A-41791-0002_1x02_P3.96mm_Vertical
JP1, JP2: SolderJumper_2_Open; SolderJumper-2_P1.3mm_Open_Pad1.0x1.5mm
R1, R2: R; R_2512_6332Metric_Pad1.40x3.35mm_HandSolder
R3: R; R_Axial_DIN0204_L3.6mm_D1.6mm_P5.08mm_Horizontal
U1: bmr480-45-to-60vin-12vout-1300w
U2: PKU3511SPI; PKU 3500S_FPM

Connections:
+5V: C11.1, C12.1, J10.1, J11.1, R1.1, U2.7 (SENSE), U2.8 (+VO)
+12V: C1.1, C2.1, C3.1, C4.1, C5.1, C6.1, C7.1, C8.1, C9.1, C10.1, J3.1, J4.1, J6.1, J7.1, J8.2, J9.2, U1.7, U1.8, U2.1 (+VIN)
+48V: C13.1, C14.1, D1.1 (K), J1.2, U1.1
CTRL: J5.1, U1.9
DGND: J5.2, JP1.1 (A), JP2.1 (A), U1.10
GND: C1.2, C2.2, C3.2, C4.2, C5.2, C6.2, C7.2, C8.2, C9.2, C10.2, C11.2, C12.2, C13.2, C14.2, J1.1, J3.2, J4.2, J6.2, J7.2, J8.1, J9.1, J10.2, J11.2, R2.2, R3.2, U1.2, U1.3, U1.4, U1.5, U2.2 (ON/OFF), U2.3 (-VIN), U2.4 (-VO), U2.5 (SENSE)
unnamed: D1.2 (A), R3.1
unnamed: R1.2, R2.1, U2.6 (TRIM)
SA0: JP1.2 (B), U1.15
SA1: JP2.2 (B), U1.14
SALERT: J5.4, U1.12
SCL: J5.5, U1.13
SDA: J5.3, U1.11

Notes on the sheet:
Add ESR Cacs Here!
This can be used to increase or decrease the voatage No pullup resitors will give the defult 5V See how to spec resitors on p.19
Caps speced on top of p.14
Power In from surface
48V Input Power Filtering
without the need for control signals or a switch, the RC pin can be wired directly to -In (p.21)

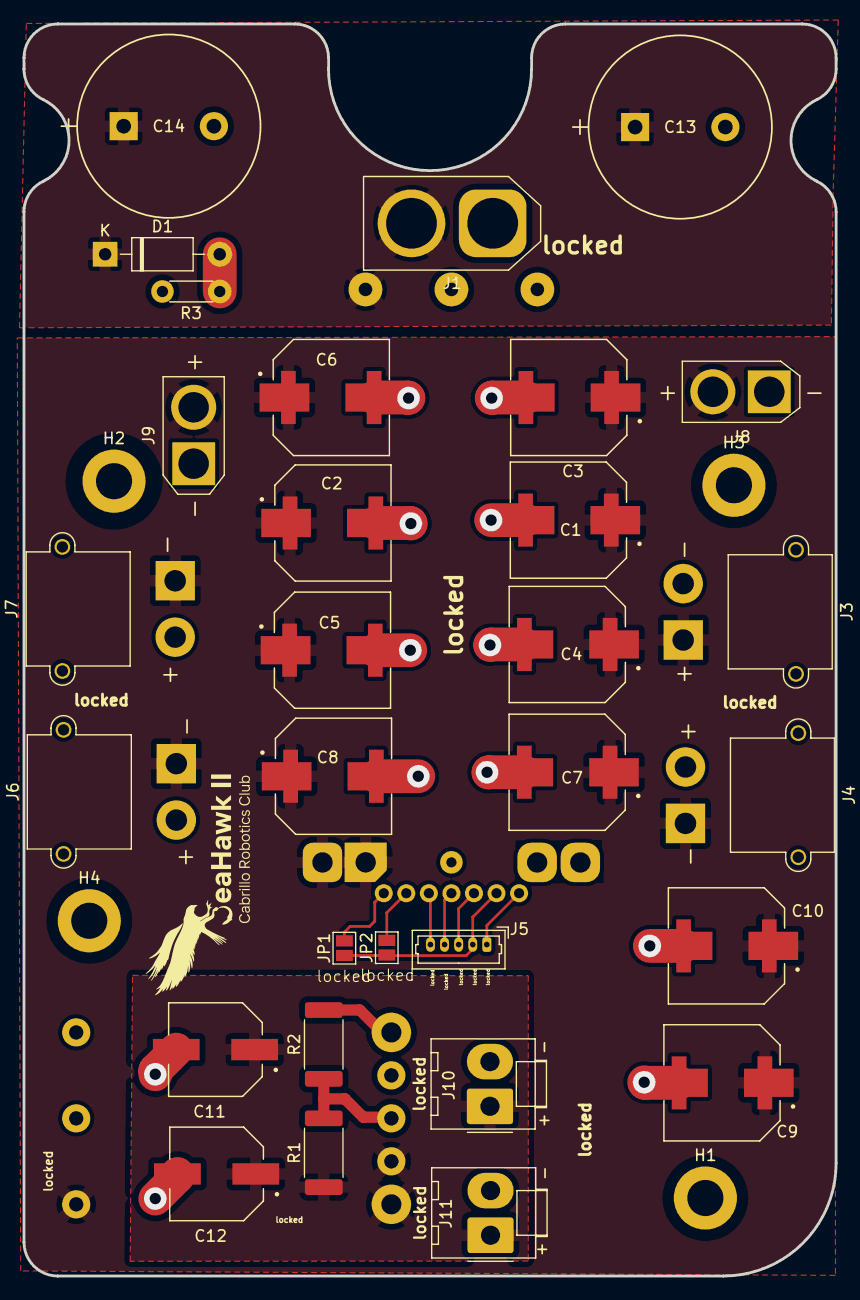
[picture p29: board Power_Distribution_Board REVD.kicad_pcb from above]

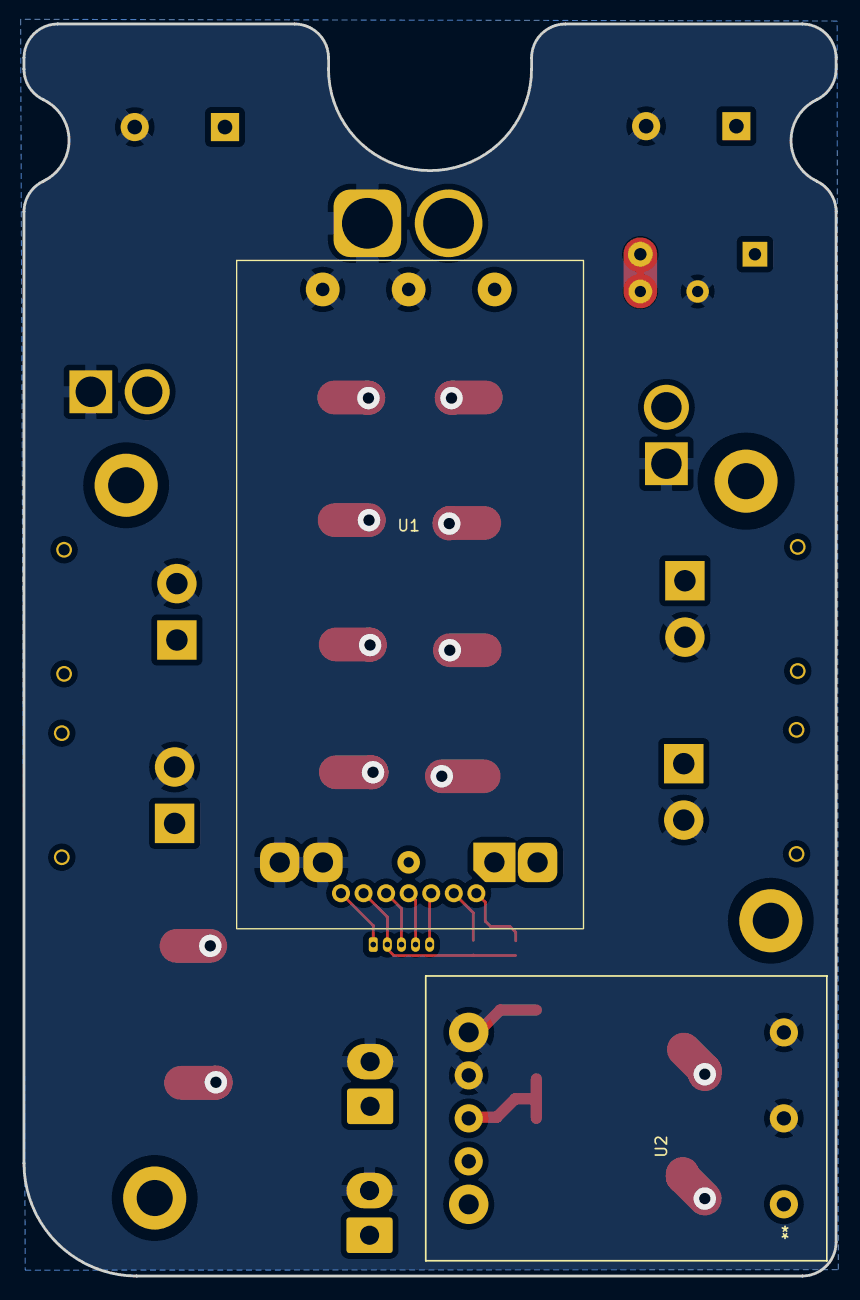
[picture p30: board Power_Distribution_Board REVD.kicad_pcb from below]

Board: 2 copper layers, 72.0 x 111.0 mm, 36 parts (2 on the bottom side), 13 nets.

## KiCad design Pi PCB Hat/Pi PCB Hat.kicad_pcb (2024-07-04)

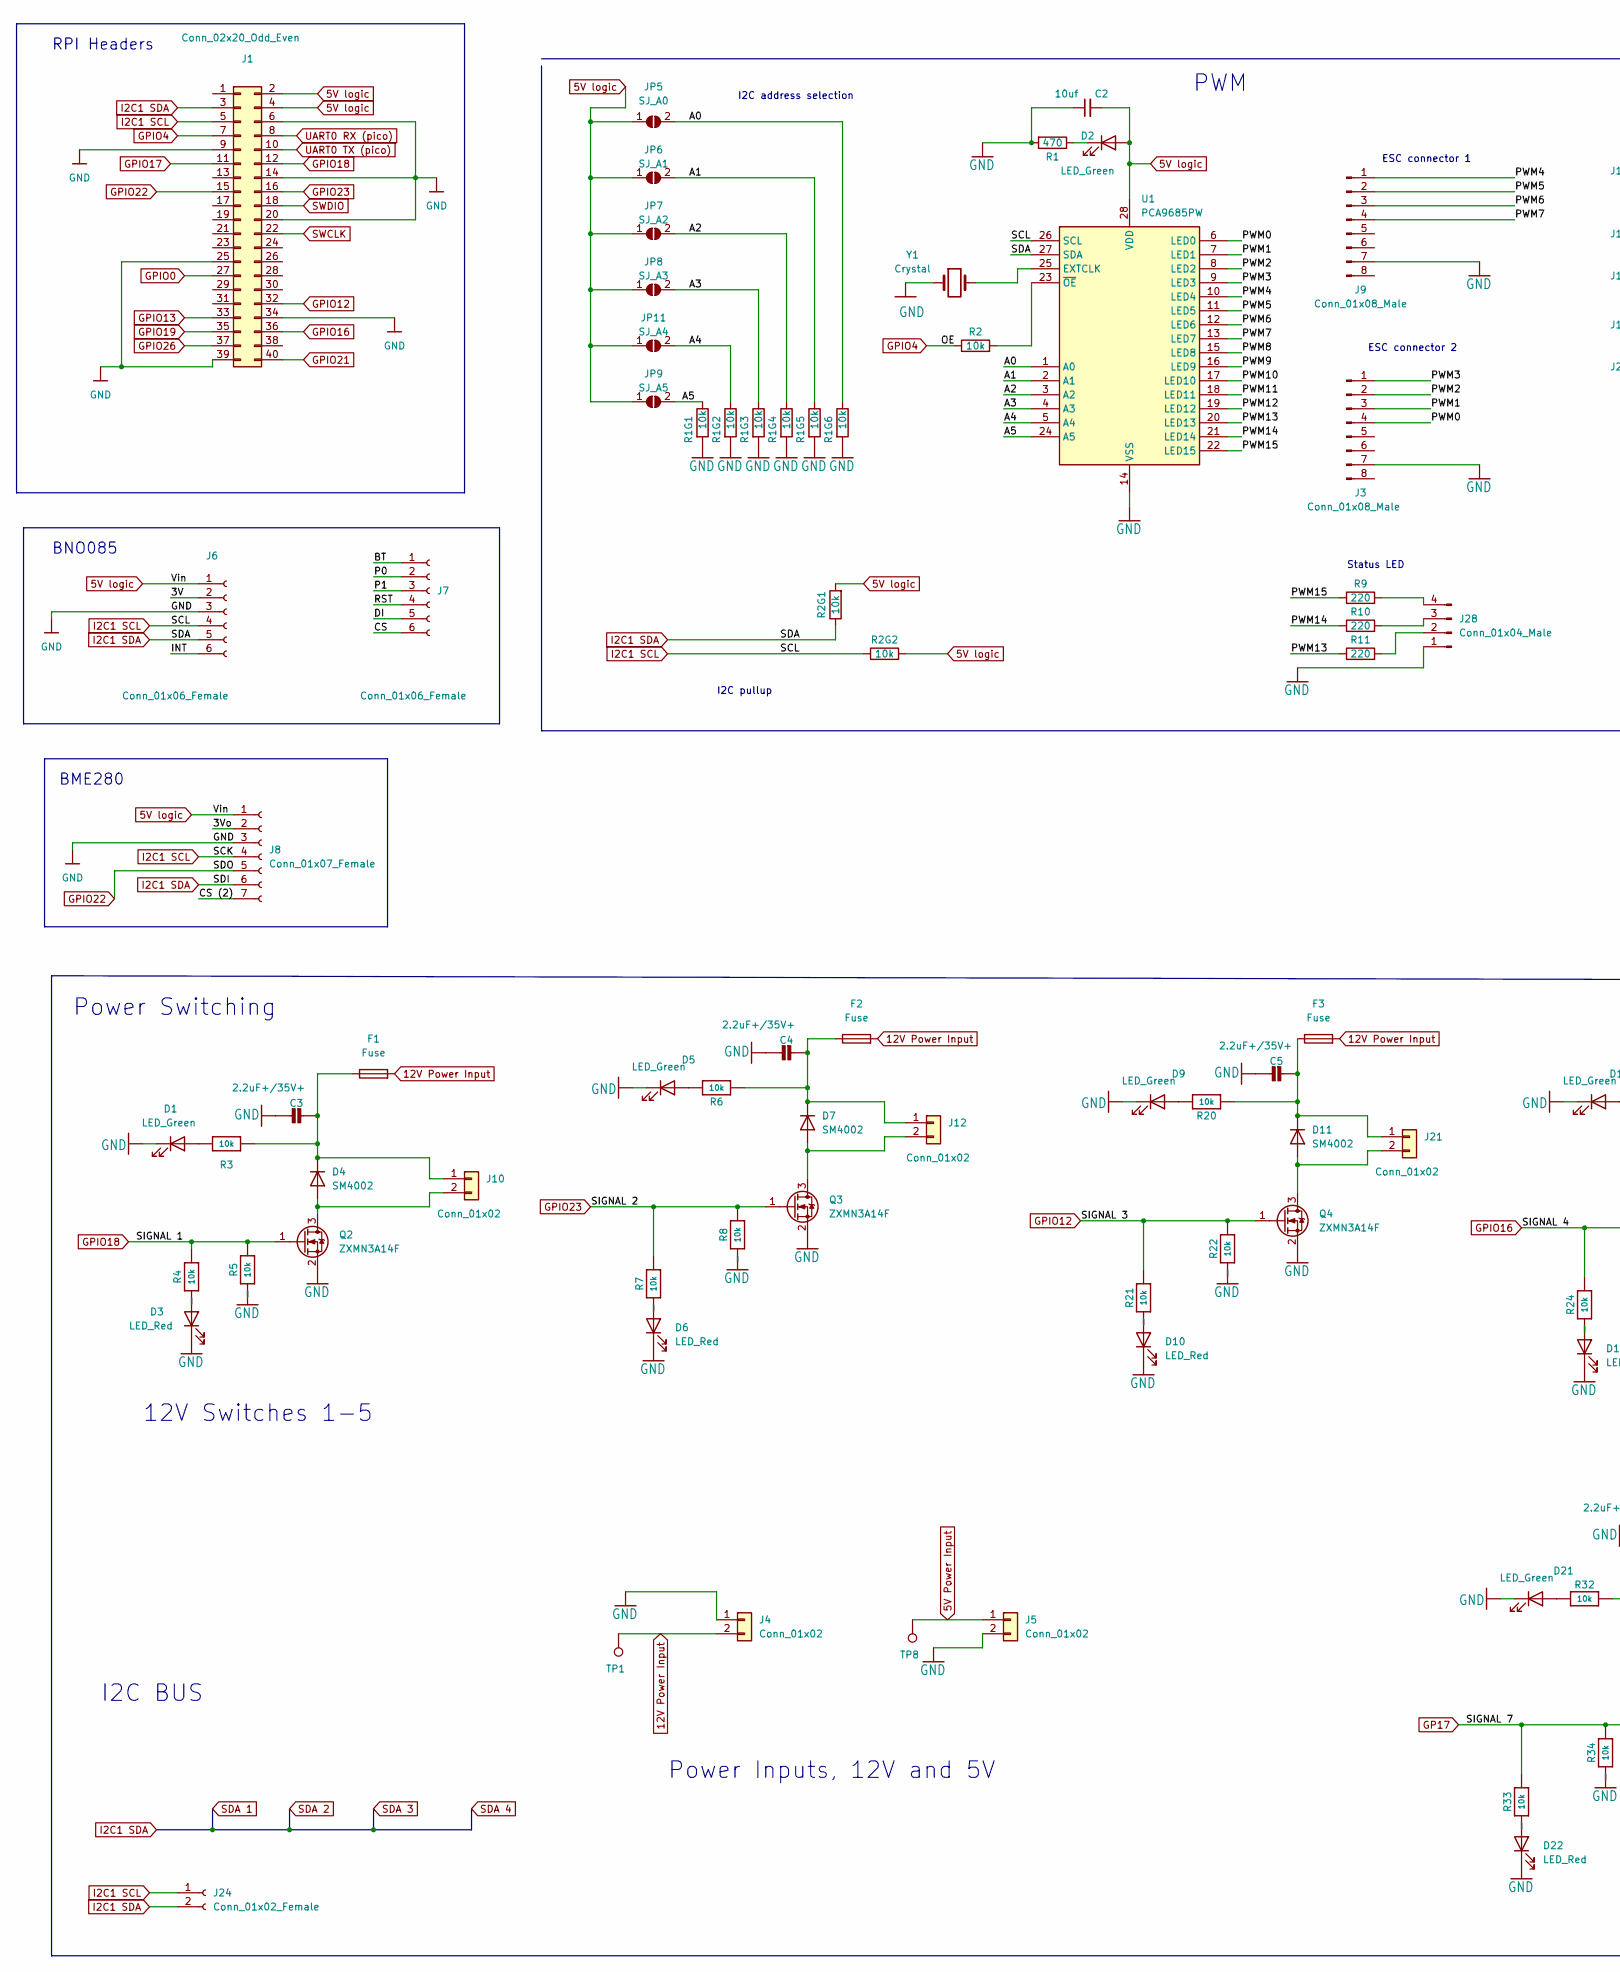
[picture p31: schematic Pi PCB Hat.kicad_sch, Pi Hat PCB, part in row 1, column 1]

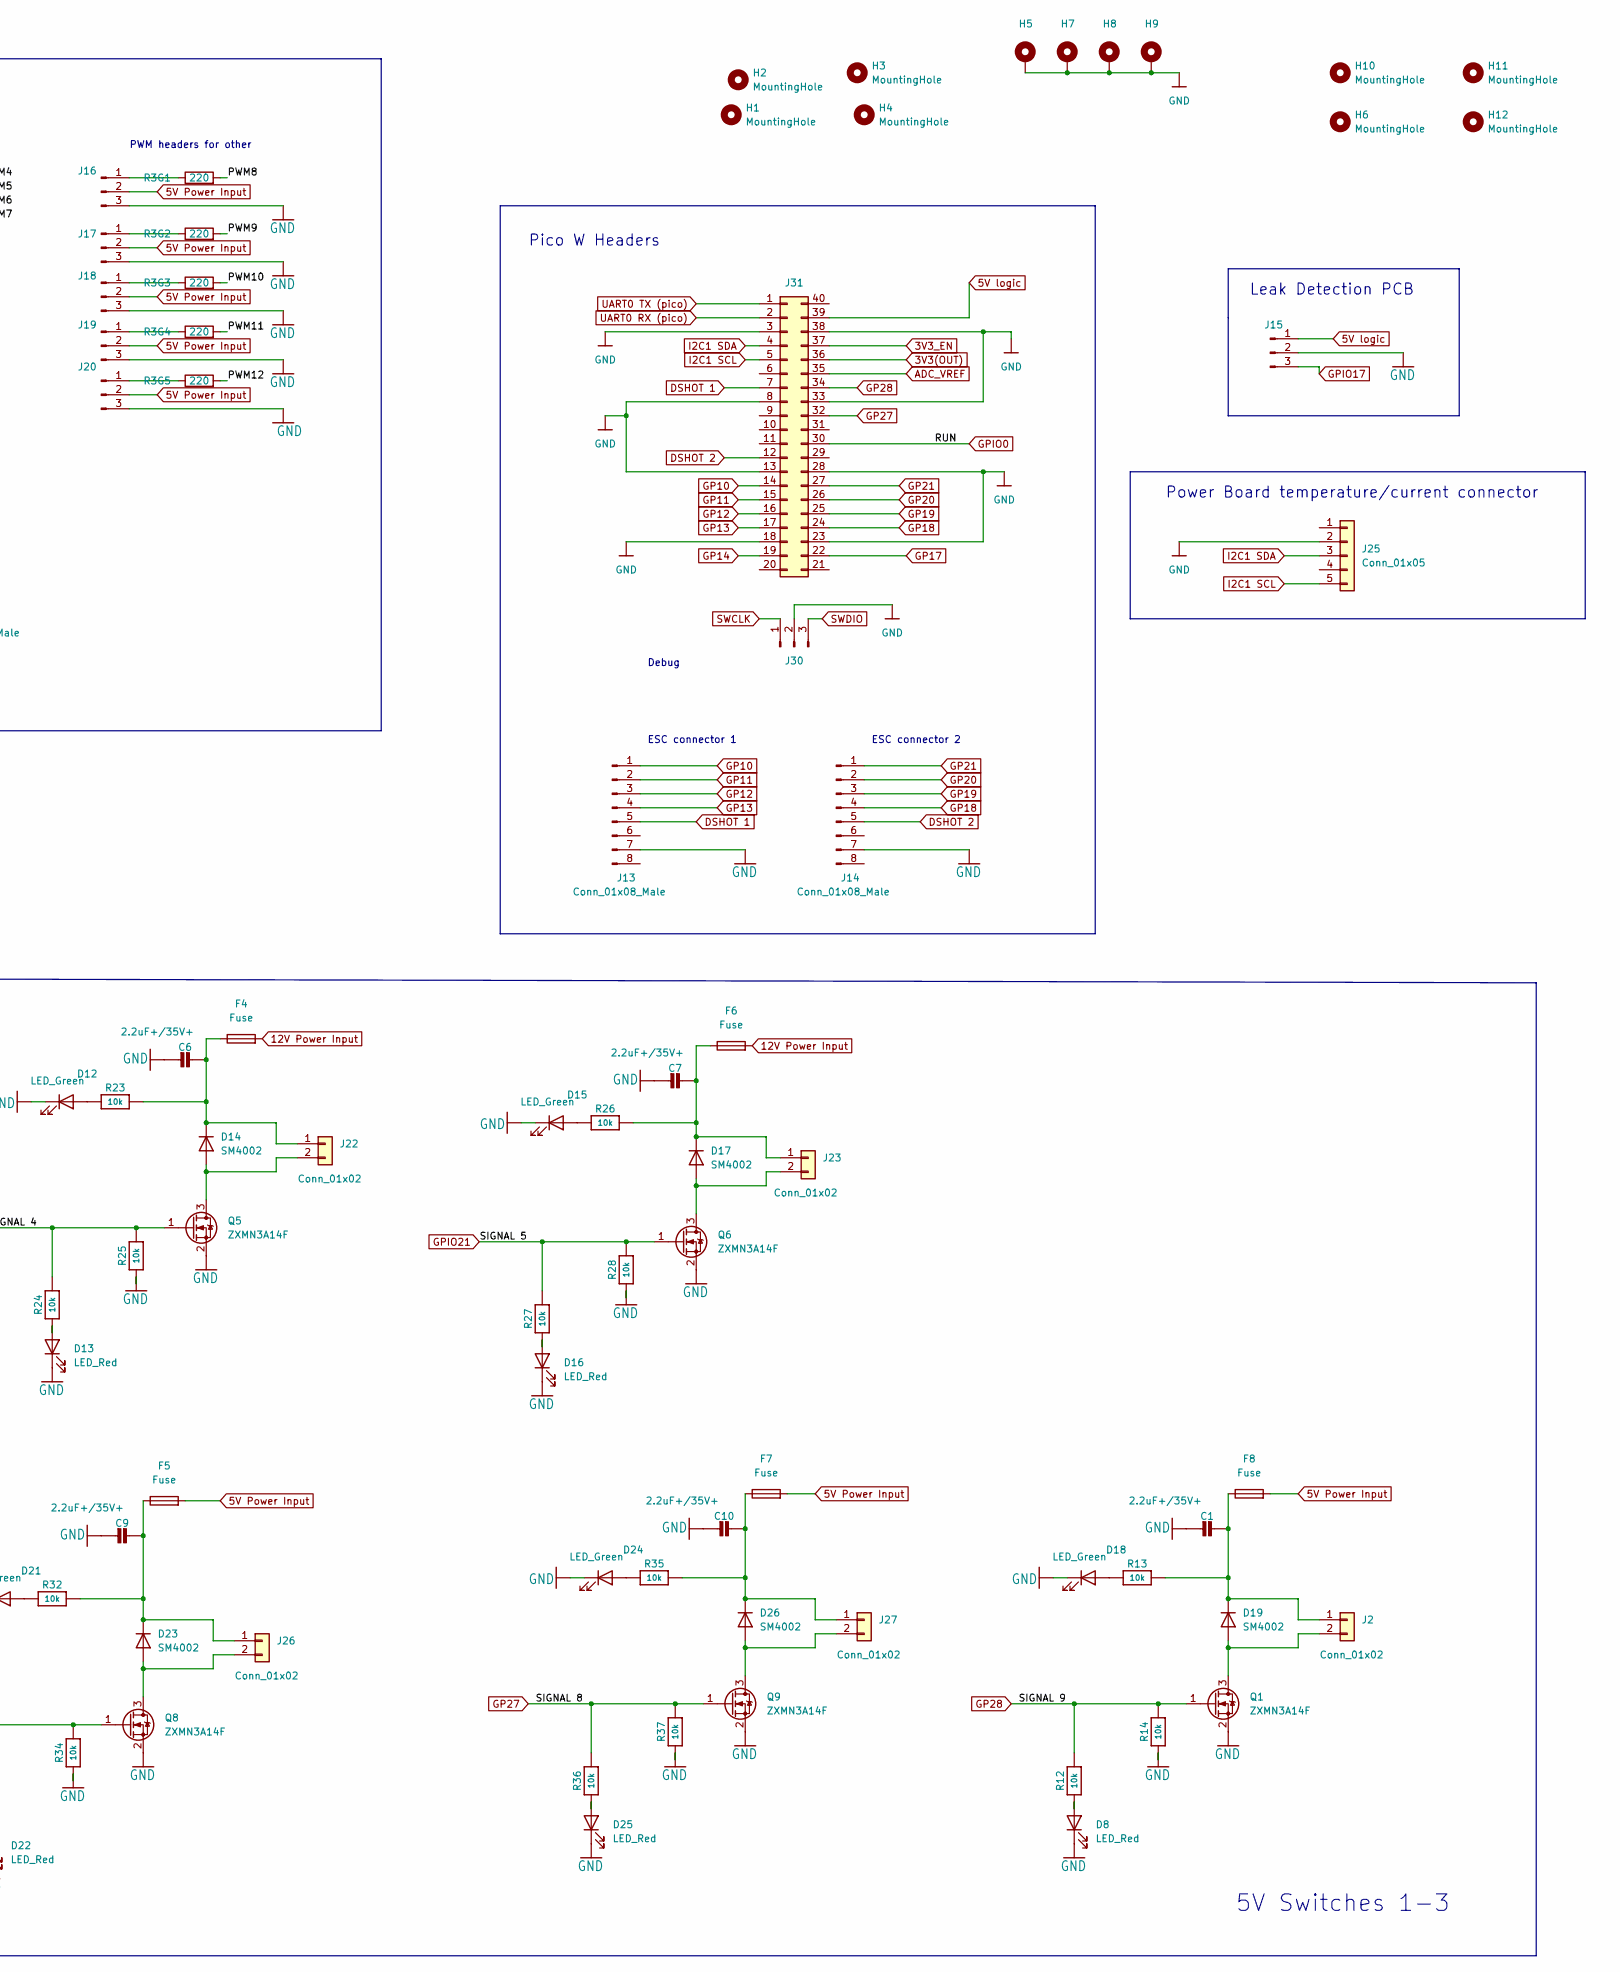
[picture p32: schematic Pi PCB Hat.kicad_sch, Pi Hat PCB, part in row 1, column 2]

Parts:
C1, C3, C4, C5, C6, C7, C9, C10: 2.2uF+/35V+; C_0805_2012Metric
C2: 10uf; C_0805_2012Metric
D1, D2, D5, D9, D12, D15, D18, D21, D24: LED_Green; LED_0603_1608Metric
D3, D6, D8, D10, D13, D16, D22, D25: LED_Red; LED_0603_1608Metric
D4, D7, D11, D14, D17, D19, D23, D26: SM4002; D_SOD-123F
F1, F2, F3, F4, F5, F6, F7, F8: Fuse; Fuse_0805_2012Metric
H1, H2, H3, H4: MountingHole; MountingHole_3.2mm_M3_DIN965_Pad
H5, H7, H8, H9: MountingHole_Pad; MountingHole_2.7mm_M2.5_DIN965_Pad
H6, H10, H11, H12: MountingHole; MountingHole_2.2mm_M2_DIN965_Pad
J1: Conn_02x20_Odd_Even; PinSocket_2x20_P2.54mm_Vertical
J2, J10, J12, J21, J22, J23, J26, J27: Conn_01x02; Molex_Micro-Latch_53253-0270_1x02_P2.00mm_Vertical_3D_model
J3, J9, J13, J14: Conn_01x08_Male; JST_SH_BM08B-SRSS-TB_1x08-1MP_P1.00mm_Vertical_3D
J4: Conn_01x02; AMASS_XT30PW-F_1x02_P2.50mm_Horizontal
J5: Conn_01x02; Molex_KK-396_A-41791-0002_1x02_P3.96mm_Vertical
J6, J7: Conn_01x06_Female; PinSocket_1x06_P2.54mm_Vertical
J8: Conn_01x07_Female; PinSocket_1x07_P2.54mm_Vertical
J15, J16, J17, J18, J19, J20: Conn_01x03_Male; PinHeader_1x03_P2.54mm_Vertical
J24: Conn_01x02_Female; PinHeader_1x02_P2.54mm_Vertical
J25: Conn_01x05; Molex_PicoBlade_53047-0510_1x05_P1.25mm_Vertical
J28: Conn_01x04_Male; Molex_PicoBlade_53047-0410_1x04_P1.25mm_Vertical
J30: Conn_01x03_Pin; PinSocket_1x03_P2.54mm_Vertical
J31: Conn_02x20_Counter_Clockwise; PinSocket_1x20_P2.54mm_Vertical
JP5: SJ_A0; SolderJumper-2_P1.3mm_Open_RoundedPad1.0x1.5mm
JP6: SJ_A1; SolderJumper-2_P1.3mm_Open_RoundedPad1.0x1.5mm
JP7: SJ_A2; SolderJumper-2_P1.3mm_Open_RoundedPad1.0x1.5mm
JP8: SJ_A3; SolderJumper-2_P1.3mm_Open_RoundedPad1.0x1.5mm
JP9: SJ_A5; SolderJumper-2_P1.3mm_Open_RoundedPad1.0x1.5mm
JP11: SJ_A4; SolderJumper-2_P1.3mm_Open_RoundedPad1.0x1.5mm
Q1, Q2, Q3, Q4, Q5, Q6, Q8, Q9: ZXMN3A14F; SOT-23
R1: 470; R_0805_2012Metric
R1G1, R1G2, R1G3, R1G4, R1G5, R1G6, R2, R2G1, R2G2, R3, R4, R5, R6, R7, R8, R12, R13, R14, R20, R21, R22, R23, R24, R25, R26, R27, R28, R32, R33, R34, R35, R36, R37: 10k; R_0805_2012Metric
R3G1, R3G2, R3G3, R3G4, R3G5, R9, R10, R11: 220; R_0805_2012Metric
TP1, TP8: TestPoint; TestPoint_Pad_1.5x1.5mm
U1: PCA9685PW; TSSOP-28_4.4x9.7mm_P0.65mm
Y1: Crystal; Crystal_HC49-U_Vertical

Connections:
3V3(OUT): J31.36
3V3_EN: J31.37
5V Power Input: F5.2, F7.2, F8.2, J5.1, J16.2, J17.2, J18.2, J19.2, J20.2, TP8.1
5V logic: C2.2, D2.2 (A), J1.2, J1.4, J6.1, J8.1, J15.1, J31.39, JP5.1 (A), JP6.1 (A), JP7.1 (A), JP8.1 (A), JP9.1 (A), JP11.1 (A), R2G1.2, R2G2.2, U1.28 (VDD)
12V Power Input: F1.2, F2.2, F3.2, F4.2, F6.2, J4.2, TP1.1; also elsewhere on the board
/3V: J6.2
/3Vo: J8.2
/A0: JP5.2 (B), R1G6.1, U1.1 (A0)
/A1: JP6.2 (B), R1G5.1, U1.2 (A1)
/A2: JP7.2 (B), R1G4.1, U1.3 (A2)
/A3: JP8.2 (B), R1G3.1, U1.4 (A3)
/A4: JP11.2 (B), R1G2.1, U1.5 (A4)
/A5: JP9.2 (B), R1G1.1, U1.24 (A5)
/BT: J7.1
/CS: J7.6
/CS (2): J8.7
/DI: J7.5
/INT: J6.6
/P0: J7.2
/P1: J7.3
/PWM0: J3.4, U1.6 (LED0)
/PWM1: J3.3, U1.7 (LED1)
/PWM2: J3.2, U1.8 (LED2)
/PWM3: J3.1, U1.9 (LED3)
/PWM4: J9.1, U1.10 (LED4)
/PWM5: J9.2, U1.11 (LED5)
/PWM6: J9.3, U1.12 (LED6)
/PWM7: J9.4, U1.13 (LED7)
/PWM8: R3G1.2, U1.15 (LED8)
/PWM9: R3G2.2, U1.16 (LED9)
/PWM10: R3G3.2, U1.17 (LED10)
/PWM11: R3G4.2, U1.18 (LED11)
/PWM12: R3G5.2, U1.19 (LED12)
/PWM13: R11.1, U1.20 (LED13)
/PWM14: R10.1, U1.21 (LED14)
/PWM15: R9.1, U1.22 (LED15)
/RST: J7.4
ADC_VREF: J31.35
DSHOT 1: J13.5, J31.7
DSHOT 2: J14.5, J31.12
GND: C1.2, C2.1, C3.2, C4.2, C5.2, C6.2, C7.2, C9.2, C10.2, D1.1 (K), D3.1 (K), D5.1 (K), D6.1 (K), D8.1 (K), D9.1 (K), D10.1 (K), D12.1 (K), D13.1 (K), D15.1 (K), D16.1 (K), D18.1 (K), D21.1 (K), D22.1 (K), D24.1 (K), D25.1 (K), H5.1, H7.1, H8.1, H9.1, J1.6, J1.9, J1.14, J1.20, J1.25, J1.34, J1.39, J3.7, J4.1, J5.2, J6.3, J8.3, J9.7, J13.7, J14.7, J15.2, J16.3, J17.3, J18.3, J19.3, J20.3, J25.2, J28.1, J30.2, J31.3, J31.8, J31.13, J31.18, J31.23, J31.28, J31.33, J31.38, Q1.2 (S), Q2.2 (S), Q3.2 (S), Q4.2 (S), Q5.2 (S), Q6.2 (S), Q8.2 (S), Q9.2 (S), R1.2, R1G1.2, R1G2.2, R1G3.2, R1G4.2, R1G5.2, R1G6.2, R5.1, R8.1, R14.1, R22.1, R25.1, R28.1, R34.1, R37.1, U1.14 (VSS), Y1.1; also elsewhere on the board
GP10: J13.1, J31.14
GP11: J13.2, J31.15
GP12: J13.3, J31.16
GP13: J13.4, J31.17
GP14: J31.19
GP17: J31.22, Q8.1 (G), R33.2, R34.2
GP18: J14.4, J31.24
GP19: J14.3, J31.25
GP20: J14.2, J31.26
GP21: J14.1, J31.27
GP27: J31.32, Q9.1 (G), R36.2, R37.2
GP28: J31.34, Q1.1 (G), R12.2, R14.2
GPIO0: J1.27, J31.30
GPIO4: J1.7, R2.1
GPIO12: J1.32, Q4.1 (G), R21.2, R22.2; also elsewhere on the board
GPIO13: J1.33
GPIO16: J1.36, Q5.1 (G), R24.2, R25.2; also elsewhere on the board
GPIO17: J1.11, J15.3
GPIO18: J1.12, Q2.1 (G), R4.2, R5.2
GPIO19: J1.35
GPIO21: J1.40, Q6.1 (G), R27.2, R28.2; also elsewhere on the board
GPIO22: J1.15, J8.5
GPIO23: J1.16, Q3.1 (G), R7.2, R8.2; also elsewhere on the board
GPIO26: J1.37
I2C1 SCL: J1.5, J6.4, J8.4, J24.1, J25.5, J31.5, R2G2.1, U1.26 (SCL)
I2C1 SDA: J1.3, J6.5, J8.6, J24.2, J25.3, J31.4, R2G1.1, U1.27 (SDA)
unnamed: D1.2 (A), R3.1
unnamed: D2.1 (K), R1.1
unnamed: D3.2 (A), R4.1
unnamed: D4.2 (A), J10.2, Q2.3 (D)
unnamed: C3.1, D4.1 (K), F1.1, J10.1, R3.2
unnamed 72: D5.2 (A), R6.1; also elsewhere on the board
unnamed 73: D6.2 (A), R7.1; also elsewhere on the board
unnamed 74: D7.2 (A), J12.2, Q3.3 (D); also elsewhere on the board
unnamed 75: C4.1, D7.1 (K), F2.1, J12.1, R6.2; also elsewhere on the board
unnamed: D8.2 (A), R12.1
unnamed: D9.2 (A), R20.1
unnamed 78: D10.2 (A), R21.1; also elsewhere on the board
unnamed: D11.2 (A), J21.2, Q4.3 (D)
unnamed 80: C5.1, D11.1 (K), F3.1, J21.1, R20.2; also elsewhere on the board
unnamed: D12.2 (A), R23.1
unnamed 82: D13.2 (A), R24.1; also elsewhere on the board
unnamed: D14.2 (A), J22.2, Q5.3 (D)
unnamed 84: C6.1, D14.1 (K), F4.1, J22.1, R23.2; also elsewhere on the board
unnamed: D15.2 (A), R26.1
unnamed 86: D16.2 (A), R27.1; also elsewhere on the board
unnamed: D17.2 (A), J23.2, Q6.3 (D)
unnamed 88: C7.1, D17.1 (K), F6.1, J23.1, R26.2; also elsewhere on the board
unnamed: D18.2 (A), R13.1
unnamed: D19.2 (A), J2.2, Q1.3 (D)
unnamed: C1.1, D19.1 (K), F8.1, J2.1, R13.2
unnamed: D21.2 (A), R32.1
unnamed: D22.2 (A), R33.1
unnamed: D23.2 (A), J26.2, Q8.3 (D)
unnamed: C9.1, D23.1 (K), F5.1, J26.1, R32.2
unnamed: D24.2 (A), R35.1
unnamed: D25.2 (A), R36.1
unnamed: D26.2 (A), J27.2, Q9.3 (D)
unnamed: C10.1, D26.1 (K), F7.1, J27.1, R35.2
unnamed: J16.1, R3G1.1
unnamed: J17.1, R3G2.1
unnamed: J18.1, R3G3.1
unnamed: J19.1, R3G4.1
unnamed: J20.1, R3G5.1
unnamed: J28.2, R11.2
unnamed: J28.3, R10.2
unnamed: J28.4, R9.2
unnamed: U1.25 (EXTCLK), Y1.2
unnamed: R2.2, U1.23 (~OE)
SWCLK: J1.22, J30.1
SWDIO: J1.18, J30.3
UART0 RX (pico): J1.8, J31.2
UART0 TX (pico): J1.10, J31.1

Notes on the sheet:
Power Switching
I2C BUS
I2C pullup
Debug
ESC connector 2
Status LED
5V Switches 1-3
12V Switches 1-5
Leak Detection PCB
I2C address selection
ESC connector 1
RPI Headers
PWM
BME280
Pico W Headers
Power Inputs, 12V and 5V
PWM headers for other
Power Board temperature/current connector
BNO085

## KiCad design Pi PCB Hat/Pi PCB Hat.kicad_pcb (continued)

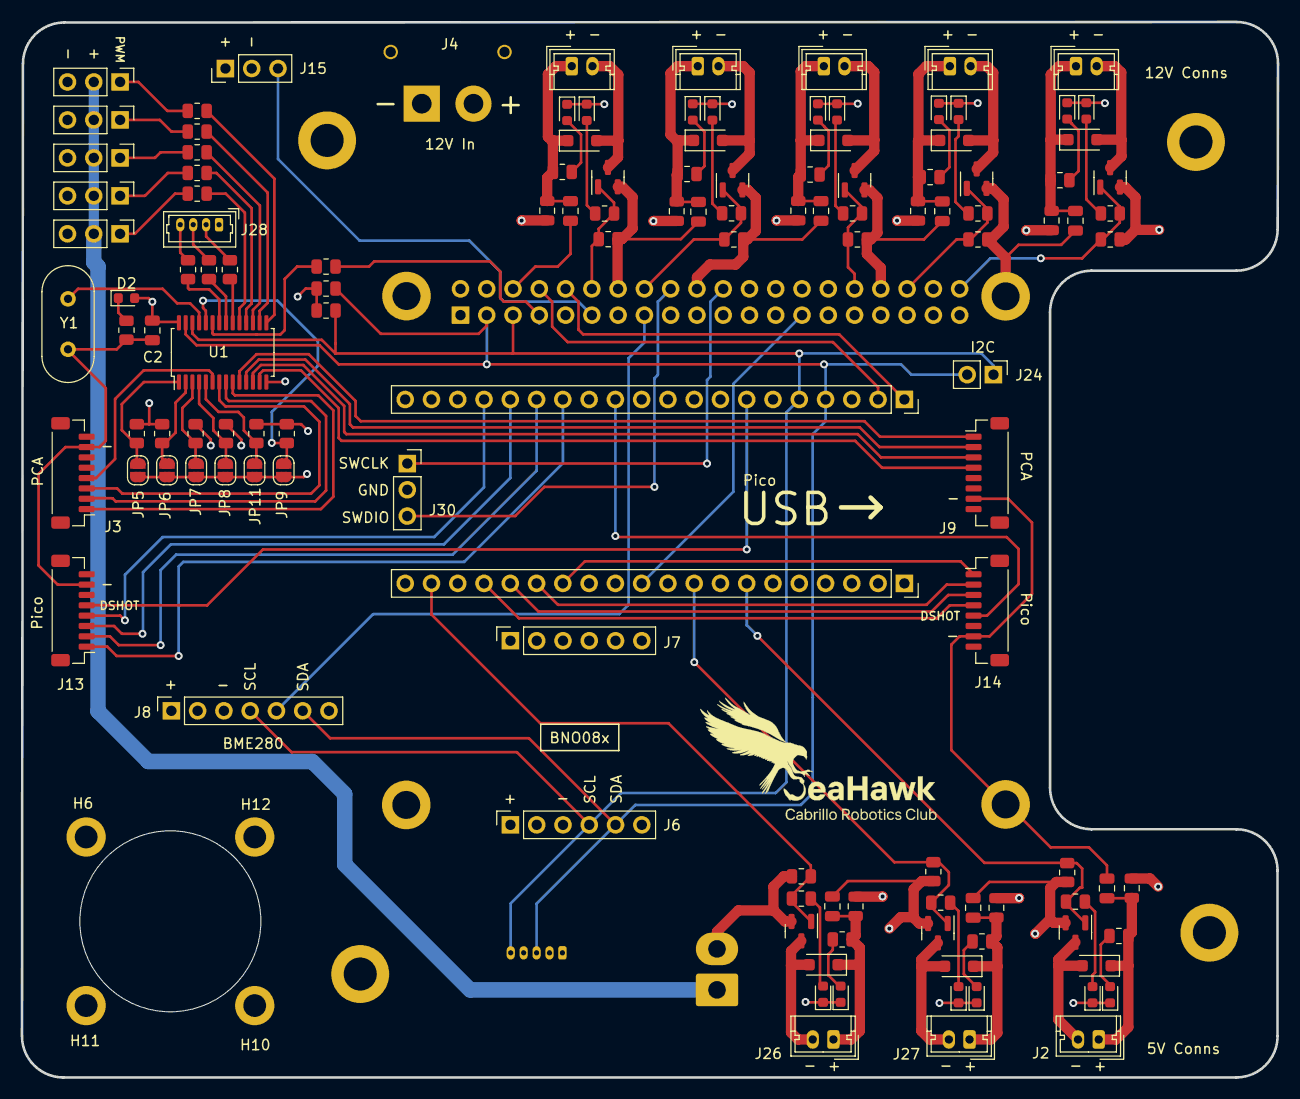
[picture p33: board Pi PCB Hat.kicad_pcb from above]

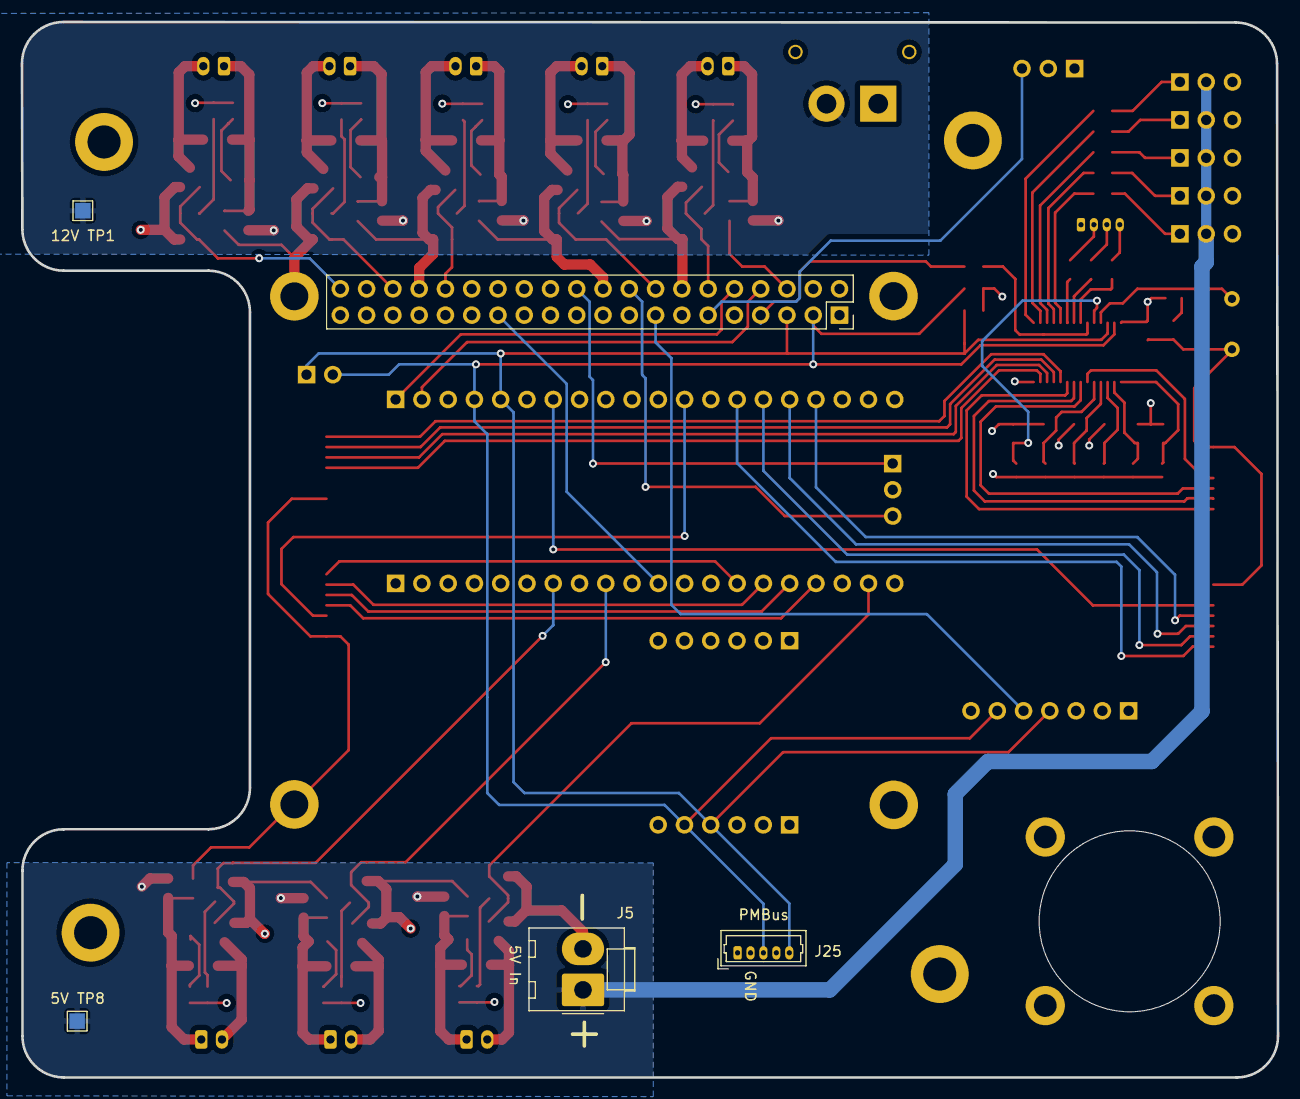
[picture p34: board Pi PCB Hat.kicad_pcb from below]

Board: 4 copper layers, 121.4 x 102.0 mm, 143 parts (5 on the bottom side), 97 nets.

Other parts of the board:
locked: 2.2uF+/35V+; C_0805_2012Metric
locked#2, locked#3, locked#4, locked#7, locked#12: 10k; R_0805_2012Metric
locked#5, locked#9, locked#10: Fuse; Fuse_0805_2012Metric
locked#6: ZXMN3A14F; SOT-23
locked#8, locked#11: 2.2uF+/35V+; C_0805_2012Metric

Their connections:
12V Power Input: locked#5.2, locked#9.2, locked#10.2; also elsewhere on the board
GND: locked.2, locked#6.2 (S), locked#8.2, locked#11.2; also elsewhere on the board
GPIO12: locked#2.2; also elsewhere on the board
GPIO16: locked#12.2; also elsewhere on the board
GPIO21: locked#7.2; also elsewhere on the board
GPIO23: locked#3.2, locked#6.1 (G); also elsewhere on the board
unnamed 72: locked#4.1; also elsewhere on the board
unnamed 73: locked#3.1; also elsewhere on the board
unnamed 74: locked#6.3 (D); also elsewhere on the board
unnamed 75: locked#4.2; also elsewhere on the board
unnamed 78: locked#2.1; also elsewhere on the board
unnamed 80: locked.1, locked#5.1; also elsewhere on the board
unnamed 82: locked#12.1; also elsewhere on the board
unnamed 84: locked#9.1, locked#11.1; also elsewhere on the board
unnamed 86: locked#7.1; also elsewhere on the board
unnamed 88: locked#8.1, locked#10.1; also elsewhere on the board

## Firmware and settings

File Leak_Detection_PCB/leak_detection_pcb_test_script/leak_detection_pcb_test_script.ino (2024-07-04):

#include <OneWire.h>
#include <Arduino.h>

int sensorPin = A0; // need to add AtoD conveter on next rev to clean things up
int sensorValue = 0;
int percent = 0;


int convertToPercent(int value);
void printValuesToSerial();

void setup() {
  // put your setup code here, to run once:
  Serial.begin(9600);
}

void loop() {
  // put your main code here, to run repeatedly:
  sensorValue = analogRead(sensorPin);
  percent = convertToPercent(sensorValue);
  printValuesToSerial();
  delay(1000);
}

int convertToPercent(int value) {
  int percentValue = map(value, 1023, 465, 0, 100);
  return percentValue;
}

void printValuesToSerial() {
  Serial.print("Sensor Value: ");
  Serial.print(sensorValue);
  Serial.print(", Percent: ");
  Serial.println(percent);
}

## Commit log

2024-07-04 pi hat pcb
    [Pi PCB Hat BOM final - Sheet1.csv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]
2024-07-04 added power distrubtion board
    [Power Board BOM.xlsx, Power_Distribution_Board REVD.kicad_pcb, Power_Distribution_Board REVD.kicad_sch]
2024-07-04 added esc carrier board and added detail to power board BOM
    [Lumenier_Carrier_Board.csv, Lumenier_Carrier_Board.kicad_pcb, Lumenier_Carrier_Board.kicad_sch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]
2024-07-04 add leak sensor board(s)
    [Leak_Detection_PCB-B_Cu.gbr, Leak_Detection_PCB-B_Mask.gbr, Leak_Detection_PCB-B_Paste.gbr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]
2024-07-06 Add schematic PDF and update KiCad schematic for Power Distribution Board
    [Power_Distribution_Board REVD.kicad_sch]
2024-08-21 added archived componet libareys
    [009484028.stp, 0530470510.step, 16SVPG330MX.step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]
